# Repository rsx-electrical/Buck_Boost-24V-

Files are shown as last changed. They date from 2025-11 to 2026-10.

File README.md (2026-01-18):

# Buck_Boost
Designed to provide a regulated 24V output from a 6S (24V nominal) battery pack with an input range of about 19–25V.
Intended for use in a rover system powering comms hardware (TpLink POE; JETSON AGX ORIN).

# Workflow
1. Message Discord that you are working in the repo. Nobody else can work on it once you message.
2. `git clone git@github.com:rsx-electrical/Buck_Boost-24V-.git`
3. Edit 4_switch_Buck_Boost
4. Edit the README in 4_switch_Buck_Boost to describe what your commit does and why the changes were made.
5. Save a zip file version of your finished work into History Folder. 
- File should named `<date/time>_<name>_<brief_description_of_changes>`
5. Stage the files you want to commit. See "How to commit changes" bellow. 
6. `git commit -m <commit message>`
7. `git push`
8. Yay:). You are done

# Specs 
Vin: 19–25V (6S Li-ion pack)
Vout: 24V nominal
Estimated power: 100W total (More than sum of both loads, some margin for overhead and future changes)

# Notes
Design is still in development; input range, component choices, and power ratings may change. Focus is on stable 24V output, good efficiency, and reliable operation in a mobile rover environment.Future updates will include board revisions, layout improvements, and performance testing.

# How to commit changes
A file with changes can be in one of three states: untracked, modified, or staged. Only staged files are included in the next commit. 
- `git status`: command to see the status of the files you have modified
## Staged files
Staged changes are changes in files that have been marked in git to be included in the next commit. The section labeled "Changes to be committed" in git status shows these staged files.
If you stage a file and then make additional changes to it, those new changes are not staged and will not be included in the next commit. To include them, you need to stage the file again.
- `git add <file_name> `: command to stage a file
- `git add . `: stage all files with changes in them. Be careful as this will also stage untracked files which often we do not want to be staged. 
- `git restore --staged <file>` : command to unstage a file
## Tracked Files
Tracked files are files that git is already monitoring for changes, meaning they were previously committed and git keeps track of any modifications to them. 
## Untracked files
Untracked files are files in your working directory that Git does not yet know about. These are sometimes autogenerated files or files for certain settings in your local repo. An example on a Mac is .DS_Store. This .DS_Store file s a hidden file created by macOS in folders to store custom metadata about that folder, like icon positions, view settings, and window size. This is not a file that we want pushed to the remote repository.

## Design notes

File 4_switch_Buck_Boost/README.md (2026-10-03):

# Purpose of readme

This README describes each commit made to the `4_switch_Buck_Boost folder`. Add the most recent changes at the top, but below this "Purpose of readme" section.
Each commit section title in this README should follow this format: `Date, Name, Title of Commit`

## 10-02 William -- SW1, GND, Vout, pores

Draw and filled all the pores above along with the vias.

## 09-22 Maria -- Rsense footprint

Added Littelfuse L4CL2512 footprint for the sensing resistors. Reangered power path to accommodate size change in new resistor and inductor footprints.

## 09-20, William -- 4 Layers GND and GNDA plane

Made all the 4 Layers, Top-GND&GNDA-Vin-GND. Connected both GND and GNDA together thorugh a via and shorted resistor to prevent DRC error. Has connected all the vias in analog stage.

## 09-19, William -- Update footprint, Analog traces

Updated FETs symbols footprints, Inductor footprints, Connect traces for analog stage

## 09-12, Maria -- Reverse Polarity Protection

Added reverse polarity protection to the schematic and layout. Placed between the fuse and vin.

## 07-17, Anthony -- Template Starting Changes

Went ahead and hunkered down on some more final changes to the analog component placement, providing a tighter, more optimized orientation for building traces, closer/more compact. Def mess around with them if need be, esp the gate driver series resistors, those can go wherever you want, just pls keep the BOOTstrap caps as close as possible. With placement of analog passive components, gonna like draw gate signal traces as copper pours, up to discretion of later design review. Additionally, settled on shunt footprint/placement without compromising hot loop layout (best we gonna do, had to sacrifice snub filter, but this is optional, pick them up later). And, upgraded inductor footprint to be more 'on-brand' with the power inductors you're likely gonna find for the necessary L (uH) values that 55V/0.55A, 12V/5A are gonna demand. Please feel more than free to change any footprints you see fit. Also, omitted the fan control aux circuit, this is gonna be external to the buck-boost pcb. TLDR: slightly prepared everything to turn this 24V buck-boost into a template PCB for bucking/boosting and buck-boosting for 5V,12V,24V, and 55V.

## 07-03, Maria -- Passive Components, Controller and Auxiliary Circuits

Feedback from the June 3rd commit was that the passive component circuits should be closer to the controller. There is no need to have them so spread out and close to the power path as it should be good to have a trace to the power path. This update moves the feedback circuit, enable circuit and passive components for the controller to be closer to the controller. This update adds traces for these circuits (traces for within these Passive Components and Auxiliary Circuits only) as well as two pores for GNDA and GND (GND pore is the GND for the enable circuit). Please note that I know that the edges of these pores are rough. Turns out I am kinda sucky at drawing out pores. Also not there is no vias added. I am going to assume that these will be added once we agree with the component placement.

## 06-03, Maria -- Passive Components, Controller and Auxiliary Circuits

Added the passive components, controller and auxiliary Circuits to the power path

## 05-23, Maria -- First Attempt at power path

Uhm so this is written on June 3rd because I forgot. Soooooo yeah basically the title, first attempt at full power path.

## 04-03, William -- PCB components placement

Tried to minimize the Hot loops, further optimization may be required

## 03-17, Anthony -- Additional revisions on Schematic for Smooth Layout design for yall

Want to make layout go as smoothly as possible, so just went ahead and ensured all components had appropiate footprints. Also added NTC (temp control) for fan control using heat probe.

## List of stuff

-Added filter caps to Vin and Vout pin connections to LT8390

-Adjusted for larger Cout over Cin to reflect calculated sizing demands.

-Changed Inductor footprint for better saturation current rating/Irms rating, previous one was way to close to our shit, plus this footprint is way more streamlined imo

-Opt to use different footprint for shunt, kicad-preloads are fucking stinky uh uh (DOWNLOAD AND IMPORT SYMBOL AND FOOTPRINT PLEASE: https://www.snapeda.com/parts/KRL3216T4-M-R003-F-T1/Susumu/view-part/ )

-EN/UVLO needs voltage divider network for proper ENABLE, so adjusted level shifter circuit for ~1.2V to be seen at pin EN/UVLO, but still programs for undervoltage lockout when reach ~16V or so, good shutoff conditions in case BMS fucks us somehow -- It's a mandatory feature not preprogrammed like a lot of the TI chips are.

-Better probing points for observing ripple, PWM, or general signals (3 kinds of probe footprints). M3 Mounting holes added as well and dedicated Net tie for GNDA and GND (fuck with footprint if need be)

-Heatsink gonna be adhesive, fuck mounts, also made it an option to use osc freq or triangle spreading +/- 15%. Triangle spread usually better, but can introduce greater voltage ripple so we can place with it using jumper cap and 2x2 head conn setup.

-NTC for temp control fan will prob be wire that sits and probes heatsink, so just a CONN for now, we'll see, up to ya'll.

-All connections on schematic should roughly agree with where they'll go on layout (ie. BST caps near chip and not power stage)

-SMD trimmers, not bulky n shit (THT or SMD, if going near chip, SMD, if away from chip, THT/SMD).

-Snub filter 0805 caps, larger caps capable of handling transient response from fets way better than 402 or 603 so yeye, also shorter fuse holders too.

## 03-14, Anthony -- Final Check on shit

All pin connections/sizing good -- ready for layout

## 03-14, Maria Finish up pins and make it look pretty

I tried to make it look prettier. I may have failed at that but I finished up the pins;).

## 03-07, William, FeedBack loop trimmer and decoupling capacitor addition

Add a trimmer to ensure precise FB voltage of 1V, and a safety margin during tuning. Add Decoupling capacitor for stabilizing voltage.

## 03-06, Maria, LT8390 Pins

To be quite honest the most important part of this commit is probably this readme where I am documenting all of the questions I have about these pins. This commit is mostly my best guess. I hope to get clarification this Saturday ;).

### RT pin

This pin should have a resistor of 75kOhms attached to it. Question is should we have a potentiometer to ensure that we can tune to 75kOhms as all resistors will have some range of error on the resistance value.

### SS pin

All of the example applications have a value of 0.1u F. I don't understand how we determine the minimum soft-start time that we want. We don't add a resistance here because we want to hiccup safety mode, not latch off or keep running mode.

### Vc pin

I am so lost, I don't know my up from down for this pin.

### PGOOD pin

This pin is smth we could connect to an external microcontroller as indicator that the voltage has successfully reached its target. I don't think that this will probably be used. However connect to INTVcc with 100k ohms so that pin is pulled low when the FB pin is within �10 percent of the final regulation voltage. Maybe down the line we will want to connect it to smth, we could leave it hanging if we wanted. A value of 100kohms is used because that is used in all of the example application circuits.

### INTVcc pin

Tie to 4.7uF ceramic capacitor as instructed.

### SYNC/SPREAD

We don't want an external source for the switching. I think we probably want to have the mode with the 15 percent spread around internal oscillator frequency to ensure no sudden noise peaks. Tie this pin to INTVcc.

## 03-05, Maria, Capacitors !!!

Thank you Anthony for the document about filtering ringing and ripple!!! The document helped with this section a lot. Also thank you to the LT890 data sheet for going through a bit about Cin and Cout capacitances.

### Ringing Frequency

Ringing frequency of 75MHz-143MHz. 22nF will filter 30MHZ-100MHz range and 4.7nF will filter 100+MHz range. In a 4-switch buck-boost, the "Active Switching Side" moves depending on the mode (Buck or Boost). Therefore a 22 nF + 4.7 nF stack on required on both the Input and Output power rails to stay protected. At the high frequencies that ringing occurs at, the 15uH inductor between the two switching nodes is 2*pi*freq\*(15e-6). For a frequency of 100MHz this comes to an impedance of 9.5KOhms. Maybe we can consider using snub circuits on the switching nodes? May not be required as power rails are protected.

### Bulk Capacitors

Calculations for the following are seen on this spreadsheet under the Capacitance Values tab: https://docs.google.com/spreadsheets/d/1GE4mJHaV0VTMqPT8AXjkSjW_NcW0vJ0DrAooZ-j17pU/edit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

#### Cout

We want the output ripple to be at most 2 percent of the output voltage which is 0.480V. The output capacitance required to have this output ripple under boost conditions is at least 5.21uF and under buck conditions at least a 0.781uF output capacitance is required. To account for the Boost Right-Half-Plane Zero phenomenon a minimum of 57.9uF output capacitance is required. To account for voltage undershoot an output capacitance of 1.46uF is required. Therefore for the circuit to be functional an output capacitance of at least 57.9uF is required. We want low ESR. Two capacitances of 33uF can be used.

#### Cin

A Cin of at least 1.14uF is required to maintain under a input voltage ripple of 0.512V. However the input capacitance network should support a Irms current of Iout(max)/2 (see pg. 21 of LT8390 data sheet). No capacitor that small can support that large of a current. We also want a very small ESR. Therefore we should have larger capacitance values in parallel to split the current and lower ESR. For electrolytic capacitors that have smaller values their ESR is very large. Is it better to have only ceramic at the beginning. For now, I am going to put a placeholder value of three 22nF electrolytic capacitors or Cin. This will lower ESR and provide required capacitance. Ask this Saturday which type of capacitor would be best here. I feel like it would be ceramic.
####Next Steps
Next steps would be determining the exact capacitors required. Most of this is gonna be a fight of finding capacitors with low ESRs. If all falls apart can just use capacitors with higher values and have more in parallel to lower ESR (generally larger value electrolytic capacitors have lower ESRs). I am uncertain if we are just gonna use capacitors we have in stock. Smth I will have to ask Anthony.

## 02-27, Maria, High Side Switch

2N7002K: rsx nmos
BSS83P: rsx pmos only has Vds of 30V. rsx pmos is cutting it close because our vin can be 25ish. Dangerous if there are any spikes in our Vin. Chosen because it has a Vds of -60V which is very safe.
R106&R105: The Vgs of the pmos (BSS83P) is +/- 20V. Having this voltage divide means that the gate of the pmos will be half the voltage of Vin. This will allow the pmos to turn on when required but have a Vgs range of 9V to 13V when the enable pin is on and it will be around 0 when the enable pin if off. These are aat least 1.46ll safe ranges.

### Next Steps

Find the spec for the LEDs that rsx has in stock. Find out what the input voltage we will get from the microcontroller. Use this information to determine the exact values for the resistors at the gate of the nmos.

### LTSpice Simulation

#### High Side Switch Vin is 25.6V

PMOS high-side switch LTSpice schematic with Vin of 25.6V



When the enable input coming from a microcontroller (enable_vin) is set high, the enable pin (en_pin) on the LT8390 is set high. When the enable input is set low, the enable pin on the LT8390 is set low as well.



The Vgs (Vpmos_gate - Vin) and Vds (Ven_pin - Vin) of the pmos. Vgs is safe within the maximum of +/- 20V. Vds is safe with a maximum of -60V.



The Vgs (Ven_pin) and Vds (Vnmos_drain) of the nmos. Vgs is safe within the maximum of +/- 20V. Vds is safe with a maximum of 60V.



pmos Id is rated for -0.33A, nmos is rated for 320mA. Currents are in a safe range.



#### High Side Switch Vin is 18V

PMOS high-side switch LTSpice schematic with Vin of 18V.



When the enable input coming from a microcontroller (enable_vin) is set high, the enable pin (en_pin) on the LT8390 is set high. When the enable input is set low, the enable pin on the LT8390 is set low as well.



The Vgs (Vpmos_gate - Vin), Vds (Ven_pin - Vin) and Id of the pmos. Vgs is safe within the maximum of +/- 20V. Vds is safe with a maximum of -60V. Id is safe as pmos is rated for -0.33A.



The Vgs (Ven_pin) and Vds (Vnmos_drain) of the nmos. Vgs is safe within the maximum of +/- 20V. Vds is safe with a maximum of 60V.



nmos current is good.



## 02-07, Maria, Reformat to be readable

Reformat to be split up into sections like the example Anthony gave us of a past boost converter. Input filtering capacitors with no values. They are placeholders. Values will need to be determined and number of capacitors will need to be determined.

## 02-05, Maria, connected power path to chip

Yeah I know title doesn't make sense. Added power path (MOSFETTS and inductor) to schematic. Connected FB. Vout/Vfb = 24. Chosen resistance values are (232 + 10)/10 =24.2. The ratio is correct; however, I assume these values may be changes for resistors rsx has in storage. 603 resistors are used because low power will flow through them. Shunt resistors are used for current sensing. Again these may be replaces with resistance values for resistors we already have. The math for these values can be found in the Google doc. Capacitors for the BST1 and BST2 are 2.5uC because gate charge of MOSFETTs are 2.5e-8C and the capacitance should be 100x the gate charge. Things needed to be talked about: do we want to use shunt resistors, and what resistors do we have in stock to choose from.

## 01-17, Anthony, added selection of res and caps

Basically just put in a couple of diff types of res and caps and their respective footprints (ceramic, polarized, shunt, basic shit that we'll prob use in the future, just pay attention to what each footprint corresponding to each symbol belongs to).

603 and 805 usually for IC filtering with 805 for larger analog symbols (LDOs) and 1206 usually for bulk cap filtering of noise at input/outputs. Polarized caps used for stabilizing voltage/reducing ripple/storing energy/etc.

603 and res up usually depend on power dissipation, with the shunt being the widest and likely used for current sensing, if choose to go down this route into design, may need to change footprint, the Vishay one is overpowered and like for 0.0001ohm applications, which is, nah.

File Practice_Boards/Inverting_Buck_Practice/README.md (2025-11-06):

# Inverting Buck Practice
Inverting Buck Board using MC33063AD topology for Inverting Regualtors (3V --> -2V)

First Iteration:
OldMariaInvertBuck

Made a couple of changes, aligned the gnd and vout terminals of the screw terminal and capacitor so at to have a cleaner and wider vout/gnd copper pour, with buck having a larger Iout>Iin, so less power less internally with potetnually larger current.

Also went ahead and drew all the passive components for the IC as closer to the main body of the chip as possible, this will come into greater importance later on when working with more complicated PWM controllers, espcially with analog traces, having as close of a connection for traces conducting in the mA order succombing to greater loss the longer the distance it has to travel to communicate with the IC.

Via placemnt centralized at the capacitor (input and output, with discharge into ground requiring the greatest degree of stitching with a return path to the bottom ground layer.

Edited Second Iteration:


Tried to make the board as tight and small as possible, the modified version is not the 'best' version. You don't hvae to make additional edits, but if you chose to you absolutely can, but regardless, where do you think the board can be improved and why? If you're not sure if there can be improvements, or feel unsure to the 'why?' part of the question, please let me know on the discord.

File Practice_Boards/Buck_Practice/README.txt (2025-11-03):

Place your current progress in this folder, and ping me when you do. I'll be able to view it and make comments, and you can pull it from the GitHub and continue with any additional work, and push your final iteration.

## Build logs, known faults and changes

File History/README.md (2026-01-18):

# Workflow
For every commit where 4_switch_Buck_Boost is changed a .zip file copy of the 4_switch_Buck_Boost must be saved in the History Folder.
Make sure the changes will appear in chronological order so have the names of the .zip file as `<date/time>_<name>_<brief_description_of_changes>`. 

<01-17/10:57 PM>_<Anthony>_<put in selection of caps and res we'll prob use, with their footprints>

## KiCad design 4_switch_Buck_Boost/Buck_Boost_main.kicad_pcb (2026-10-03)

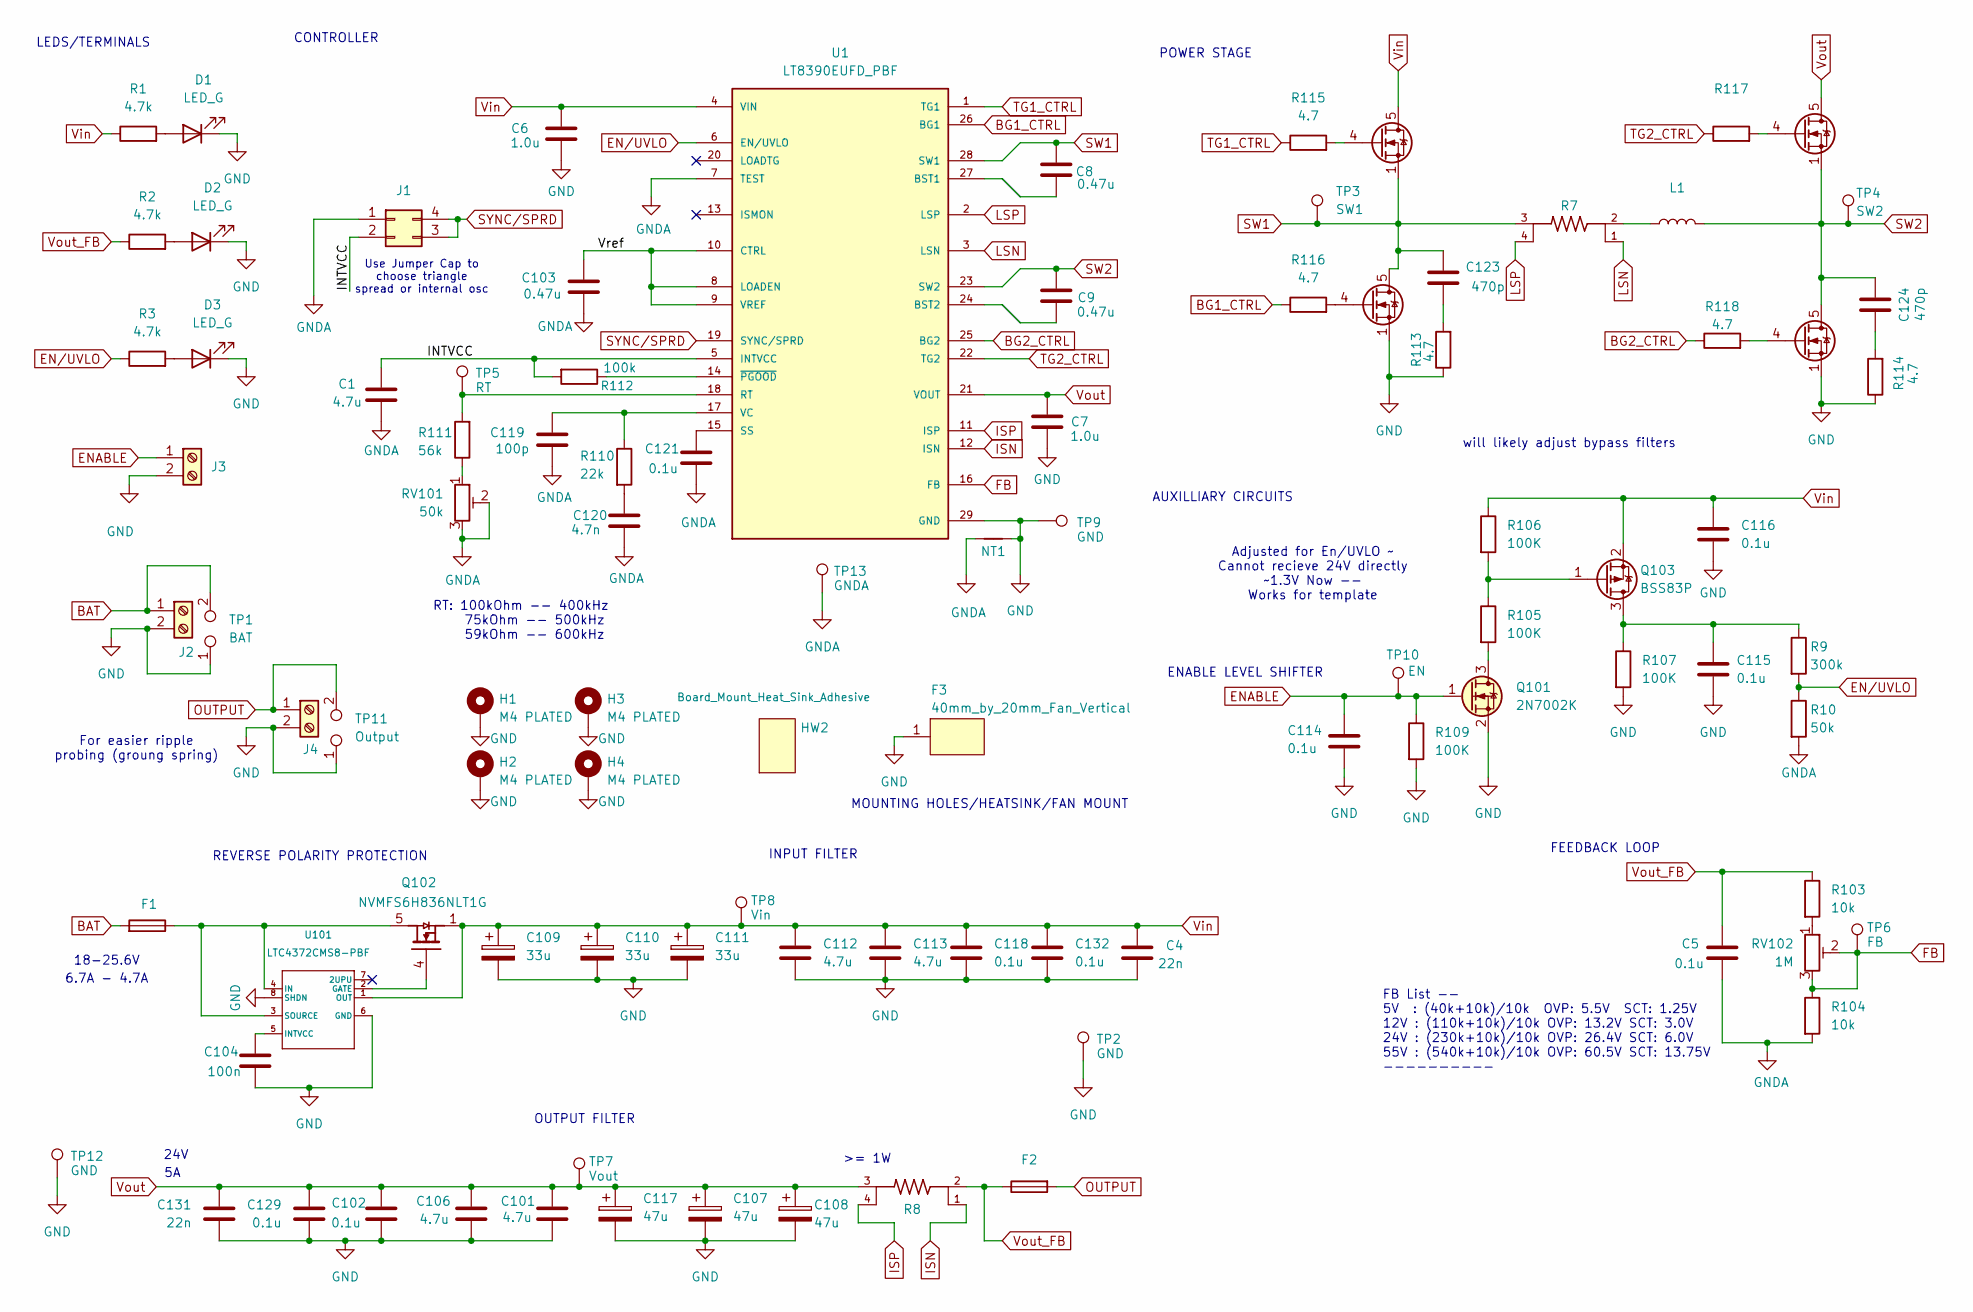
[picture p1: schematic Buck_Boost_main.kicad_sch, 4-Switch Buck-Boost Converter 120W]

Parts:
C1, C101, C106, C112, C113: 4.7u; C_0805_2012Metric
C4, C131: 22n; C_0603_1608Metric
C5, C102, C114, C115, C116, C118, C121, C129, C132: 0.1u; C_0603_1608Metric
C6, C7: 1.0u; C_0603_1608Metric
C8, C9, C103: 0.47u; C_0603_1608Metric
C104: 100n; C_0603_1608Metric
C107, C108, C117: 47u; CP_Elec_8x10.5
C109, C110, C111: 33u; CP_Elec_8x10.5
C119: 100p; C_0603_1608Metric
C120: 4.7n; C_0603_1608Metric
C123, C124: 470p; C_0805_2012Metric
D1, D2, D3: LED_G; LED_0805_2012Metric; MPN LTST-C170GKT
F1, F2: Fuse_Holder_Auto; Fuseholder_Blade_Mini_Keystone_3568; MPN 3568-10
F3: 40mm_by_20mm_Fan_Vertical; 40mmFan; MPN THA0412AD
H1, H2, H3, H4: M4 PLATED; MountingHole_3.2mm_M3_Pad_Via
HW2: Board_Mount_Heat_Sink_Adhesive; BDN10-3CB_A01; MPN BDN10-3CB/A01
J1: Conn_02x02_Counter_Clockwise; PinHeader_2x02_P1.00mm_Vertical
J2, J4: Screw_Terminal_2x5.08; Molex_0398800302; MPN 398800302
J3: Screw_Terminal_2x2.54; Wurth_691210910002; MPN 691210910002
L1: L_Bourns_SRP1770TA_16.9x16.9mm; MPN PQ2617BHA-150K
NT1: NetTie_2; NetTie-2_SMD_Pad0.5mm
Q101: 2N7002K; SOT-23; MPN 2N7002K-T1-E3
Q102: NVMFS6H836NLT1G; ONSemi_SO-8FL_488AA
Q103: BSS83P; SOT-23
Q104, Q105, Q106, Q107: BSC070N10LS5; TDSON-8-1
R1, R2, R3: 4.7k; R_0603_1608Metric
R7, R8: Littelfuse_L4CA0612_4Terminal; PARTREV N/A
R9: 300k; R_0603_1608Metric
R10: 50k; R_0603_1608Metric
R103, R104: 10k; R_0603_1608Metric
R105, R106, R107, R109: 100K; R_0603_1608Metric
R110: 22k; R_0603_1608Metric
R111: 56k; R_0603_1608Metric
R112: 100k; R_0603_1608Metric
R113, R114: 4.7; C_0805_2012Metric
R115, R116, R117, R118: 4.7; R_0603_1608Metric
RV101: 50k; Potentiometer_Bourns_3314G_Vertical
RV102: 1M; Potentiometer_Bourns_3314G_Vertical
TP1: BAT; TestPoint_2Pads_Pitch2.54mm_Drill0.8mm
TP2, TP9, TP12: GND; TestPoint_Pad_D1.0mm
TP3: SW1; TestPoint_Loop_D1.80mm_Drill1.0mm_Beaded
TP4: SW2; TestPoint_Loop_D1.80mm_Drill1.0mm_Beaded
TP5: RT; TestPoint_Pad_D1.0mm
TP6: FB; TestPoint_Pad_D1.0mm
TP7: Vout; TestPoint_Pad_D1.0mm
TP8: Vin; TestPoint_Pad_D1.0mm
TP10: EN; TestPoint_Pad_D1.0mm
TP11: Output; TestPoint_2Pads_Pitch2.54mm_Drill0.8mm
TP13: GNDA; TestPoint_Pad_D1.0mm
U1: LT8390EUFD_PBF; QFN50P500X400X80-29N; PARTREV C
U101: LTC4372CMS8-PBF; MS8_05-08-1660_ADI

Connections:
/INTVCC: C1.2, J1.2, R112.2, U1.5 (INTVCC)
/Vref: C103.2, U1.8 (LOADEN), U1.9 (VREF), U1.10 (CTRL)
BAT: F1.1, J2.1, TP1.2
BG1_CTRL: R116.1, U1.26 (BG1)
BG2_CTRL: R118.1, U1.25 (BG2)
ENABLE: C114.1, J3.1, Q101.1 (G), R109.1, TP10.1
EN/UVLO: R3.1, R9.2, R10.1, U1.6 (EN/UVLO)
FB: R104.1, RV102.2, RV102.3, TP6.1, U1.16 (FB)
GND: C4.2, C6.1, C7.1, C101.2, C102.2, C104.2, C106.2, C107.2, C108.2, C109.2, C110.2, C111.2, C112.2, C113.2, C114.2, C115.2, C116.2, C117.2, C118.2, C129.2, C131.2, C132.2, D1.1 (K), D2.1 (K), D3.1 (K), F3.1, H1.1, H2.1, H3.1, H4.1, J2.2, J3.2, J4.2, NT1.2, Q101.2 (S), Q106.1 (S), Q106.2, Q106.3, Q107.1 (S), Q107.2, Q107.3, R107.2, R109.2, R113.1, R114.1, TP1.1, TP2.1, TP9.1, TP11.1, TP12.1, U1.29 (GND), U101.6 (GND), U101.8 (SHDN)
GNDA: C1.1, C5.2, C103.1, C119.2, C120.2, C121.2, J1.1, NT1.1, R10.2, R104.2, RV101.2, RV101.3, TP13.1, U1.7 (TEST)
ISN: R8.1, U1.12 (ISN)
ISP: R8.4, U1.11 (ISP)
LSN: R7.1, U1.3 (LSN)
LSP: R7.4, U1.2 (LSP)
unnamed: C120.1, R110.2
unnamed: C123.2, R113.2
unnamed: C124.1, R114.2
unnamed: D1.2 (A), R1.2
unnamed: D2.2 (A), R2.2
unnamed: D3.2 (A), R3.2
unnamed: L1.1, R7.2
unnamed: Q101.3 (D), R105.2
unnamed: F1.2, Q102.5 (D), U101.3 (SOURCE), U101.4 (IN)
unnamed: Q102.4 (G), U101.2 (GATE)
unnamed: C115.1, Q103.3 (D), R9.1, R107.1
unnamed: Q103.1 (G), R105.1, R106.2
unnamed: Q104.4 (G), R115.2
unnamed: Q105.4 (G), R117.2
unnamed: Q106.4 (G), R118.2
unnamed: Q107.4 (G), R116.2
unnamed: R103.2, RV102.1
unnamed: R111.1, RV101.1
unnamed: C8.1, U1.27 (BST1)
unnamed: C9.1, U1.24 (BST2)
unnamed: R111.2, TP5.1, U1.18 (RT)
unnamed: C121.1, U1.15 (SS)
unnamed: C119.1, R110.1, U1.17 (VC)
unnamed: R112.1, U1.14 (~PGOOD)
unnamed: C104.1, U101.5 (INTVCC)
OUTPUT: F2.1, J4.1, TP11.2
SW1: C8.2, C123.1, Q104.1 (S), Q104.2, Q104.3, Q107.5 (D), Q107.6, Q107.7, Q107.8, R7.3, TP3.1, U1.28 (SW1)
SW2: C9.2, C124.2, L1.2, Q105.1 (S), Q105.2, Q105.3, Q106.5 (D), Q106.6, Q106.7, Q106.8, TP4.1, U1.23 (SW2)
SYNC/SPRD: J1.3, J1.4, U1.19 (SYNC/SPRD)
TG1_CTRL: R115.1, U1.1 (TG1)
TG2_CTRL: R117.1, U1.22 (TG2)
Vin: C4.1, C6.2, C109.1, C110.1, C111.1, C112.1, C113.1, C116.1, C118.1, C132.1, Q102.1 (S), Q102.2 (S), Q102.3 (S), Q103.2 (S), Q104.5 (D), Q104.6, Q104.7, Q104.8, R1.1, R106.1, TP8.1, U1.4 (VIN), U101.1 (OUT)
Vout: C7.2, C101.1, C102.1, C106.1, C107.1, C108.1, C117.1, C129.1, C131.1, Q105.5 (D), Q105.6, Q105.7, Q105.8, R8.3, TP7.1, U1.21 (VOUT)
Vout_FB: C5.1, F2.2, R2.1, R8.2, R103.1

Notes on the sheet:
LEDS/TERMINALS
Adjusted for En/UVLO ~ Cannot recieve 24V directly ~1.3V Now -- Works for template
INPUT FILTER
24V
REVERSE POLARITY PROTECTION
FB List -- 5V : (40k+10k)/10k OVP: 5.5V SCT: 1.25V 12V : (110k+10k)/10k OVP: 13.2V SCT: 3.0V 24V : (230k+10k)/10k OVP: 26.4V SCT: 6.0V 55V : (540k+10k)/10k OVP: 60.5V SCT: 13.75V ----------
18-25.6V
AUXILLIARY CIRCUITS
Use Jumper Cap to choose triangle spread or internal osc
RT: 100kOhm -- 400kHz 75kOhm -- 500kHz 59kOhm -- 600kHz
POWER STAGE
For easier ripple probing (groung spring)
FEEDBACK LOOP
OUTPUT FILTER
ENABLE LEVEL SHIFTER
will likely adjust bypass filters
CONTROLLER
6.7A - 4.7A
>= 1W
MOUNTING HOLES/HEATSINK/FAN MOUNT

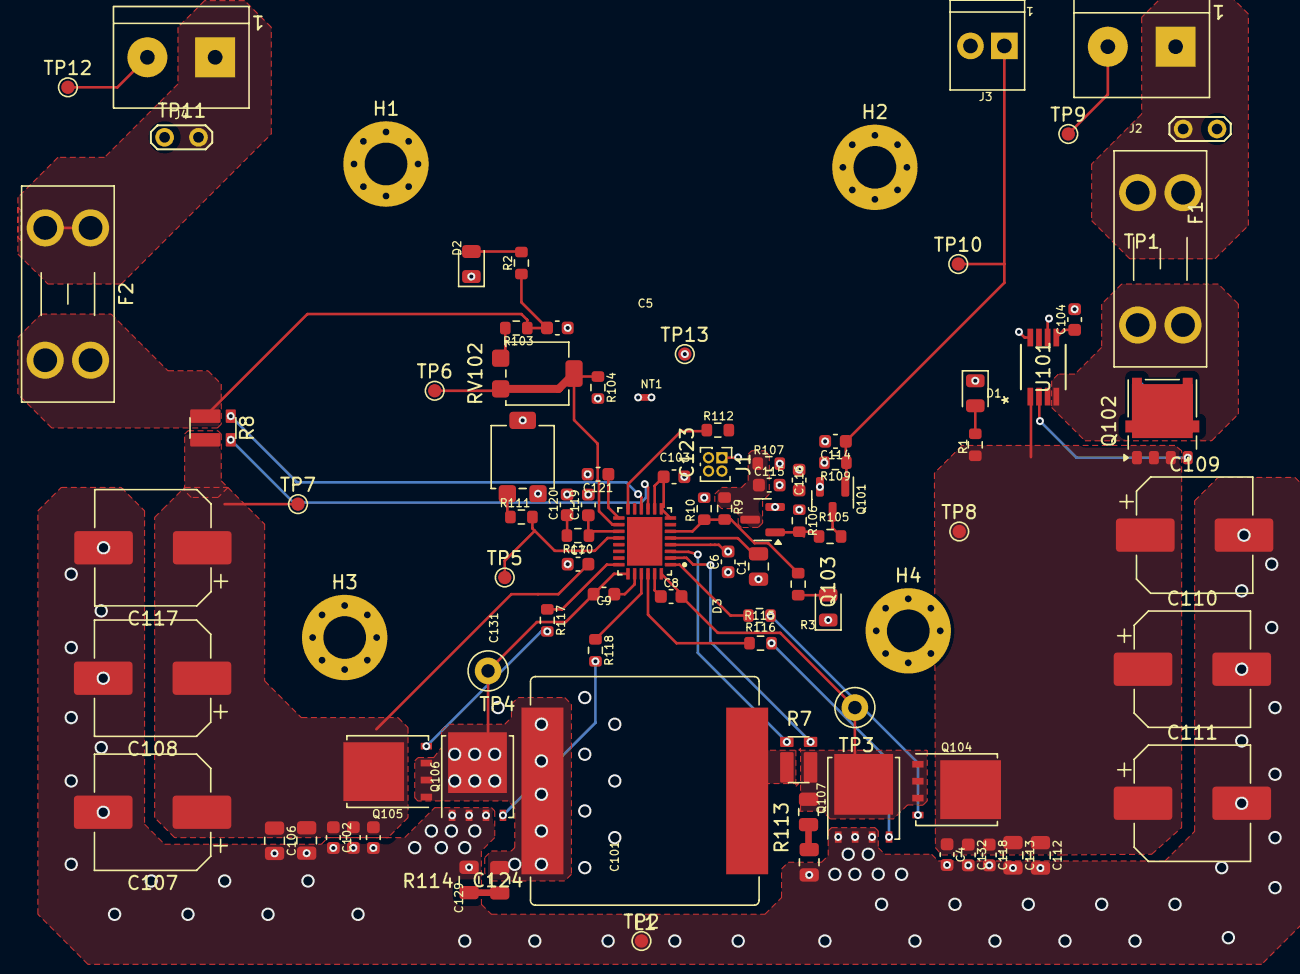
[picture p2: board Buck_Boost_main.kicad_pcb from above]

Board: 4 copper layers, 95 parts (0 on the bottom side), 48 nets.

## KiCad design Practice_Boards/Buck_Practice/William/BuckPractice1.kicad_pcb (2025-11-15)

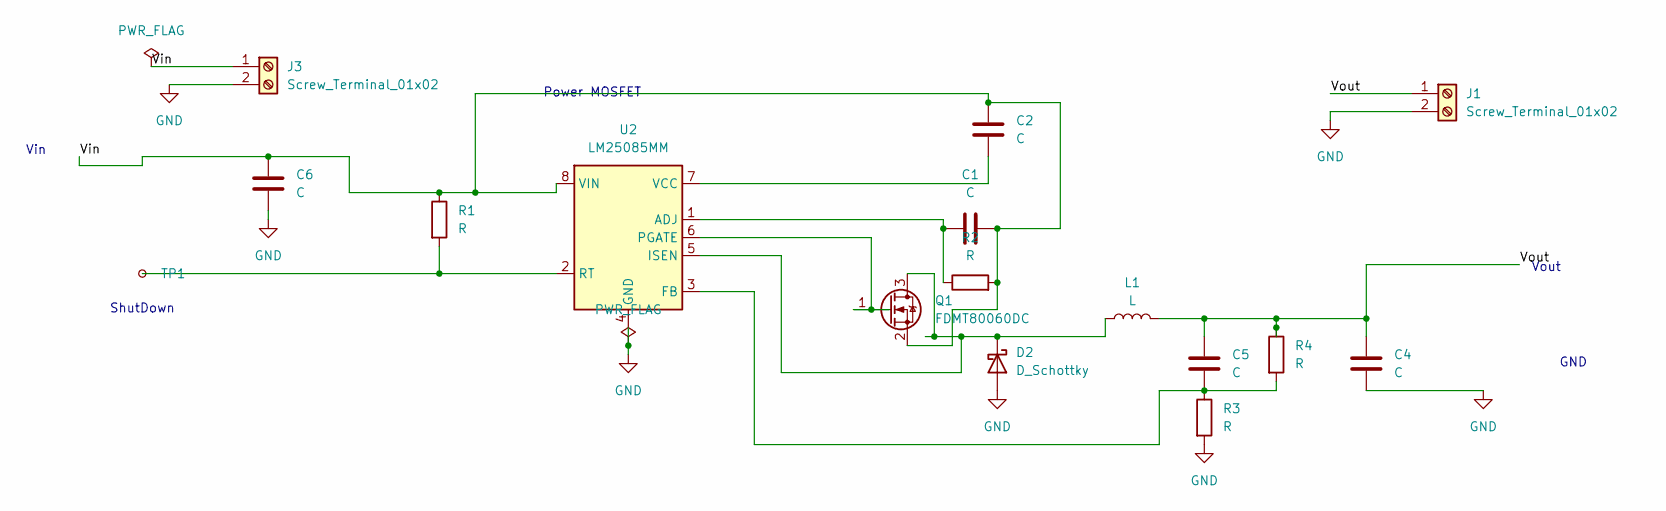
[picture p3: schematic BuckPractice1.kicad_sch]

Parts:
C1, C5: C; C_0805_2012Metric; MPN CL21B105KBFNNNE
C2, C4, C6: C; C_Elec_10x10.2
D2: D_Schottky; D_SMA
J1, J3: Screw_Terminal_01x02; TerminalBlock_4Ucon_1x02_P3.50mm_Vertical
L1: L; L_Coilcraft_XAL1350-XXX
Q1: FDMT80060DC; PQFN_8x8
R1, R2, R3, R4: R; R_0805_2012Metric
TP1: TestPoint_Small; TestPoint_Pad_D1.0mm
U2: LM25085MM; MSOP-8_3x3mm_P0.65mm

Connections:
/Vin: C1.2, C2.1, C6.1, J3.1, Q1.2 (S), R1.1, R2.2, U2.8 (VIN)
/Vout: C4.1, C5.2, J1.1, L1.2, R4.1
GND: C4.2, C6.2, D2.2 (A), J1.2, J3.2, R3.2, U2.4 (GND)
unnamed: D2.1 (K), L1.1, Q1.3 (D), U2.5 (ISEN)
unnamed: Q1.1 (G), U2.6 (PGATE)
unnamed: C1.1, R2.1, U2.1 (ADJ)
unnamed: C5.1, R3.1, R4.2, U2.3 (FB)
unnamed: R1.2, TP1.1, U2.2 (RT)
unnamed: C2.2, U2.7 (VCC)

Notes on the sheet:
GND
Vin
Vout
Power MOSFET
ShutDown

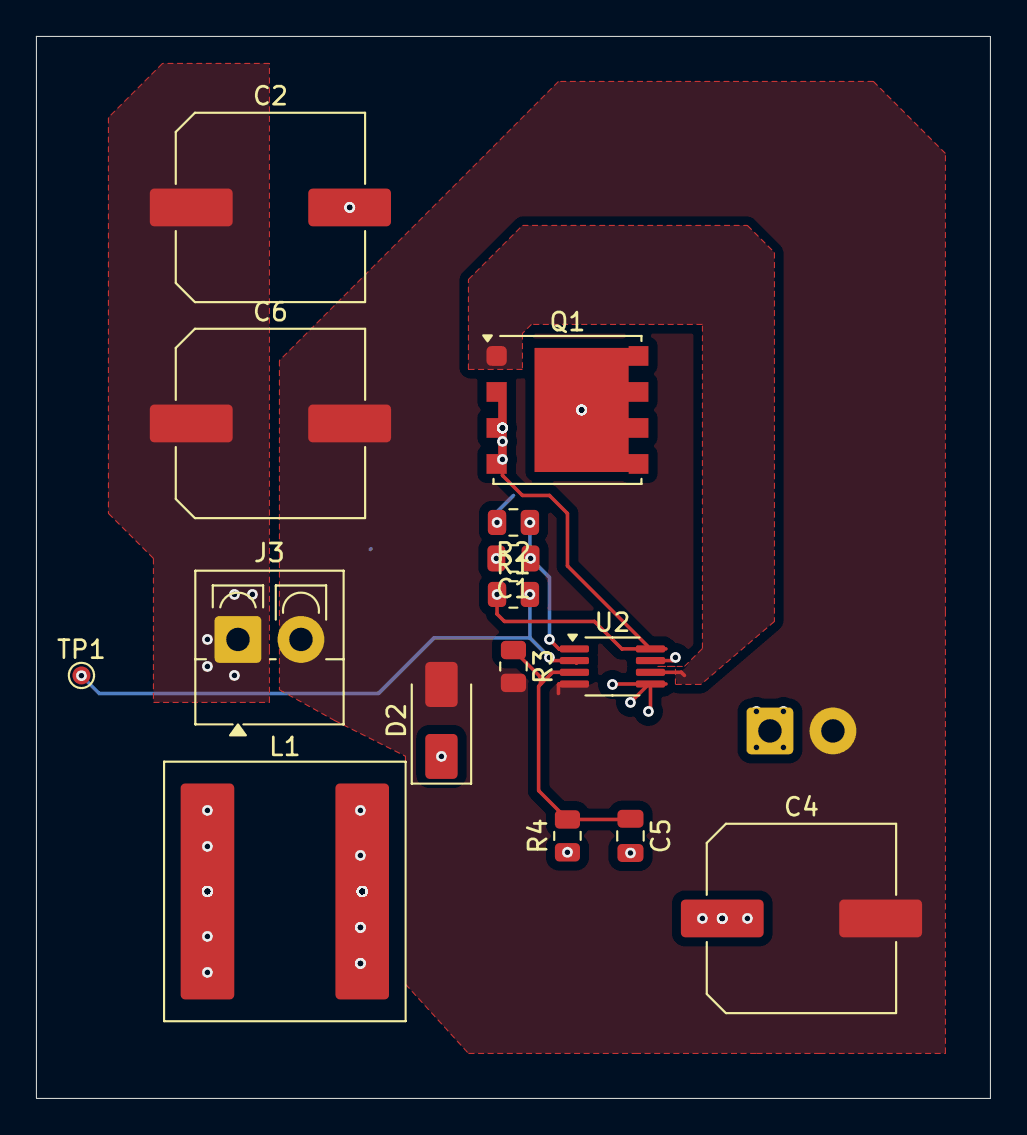
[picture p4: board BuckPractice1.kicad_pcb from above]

Board: 2 copper layers, 53.0 x 59.0 mm, 16 parts (1 on the bottom side), 9 nets.

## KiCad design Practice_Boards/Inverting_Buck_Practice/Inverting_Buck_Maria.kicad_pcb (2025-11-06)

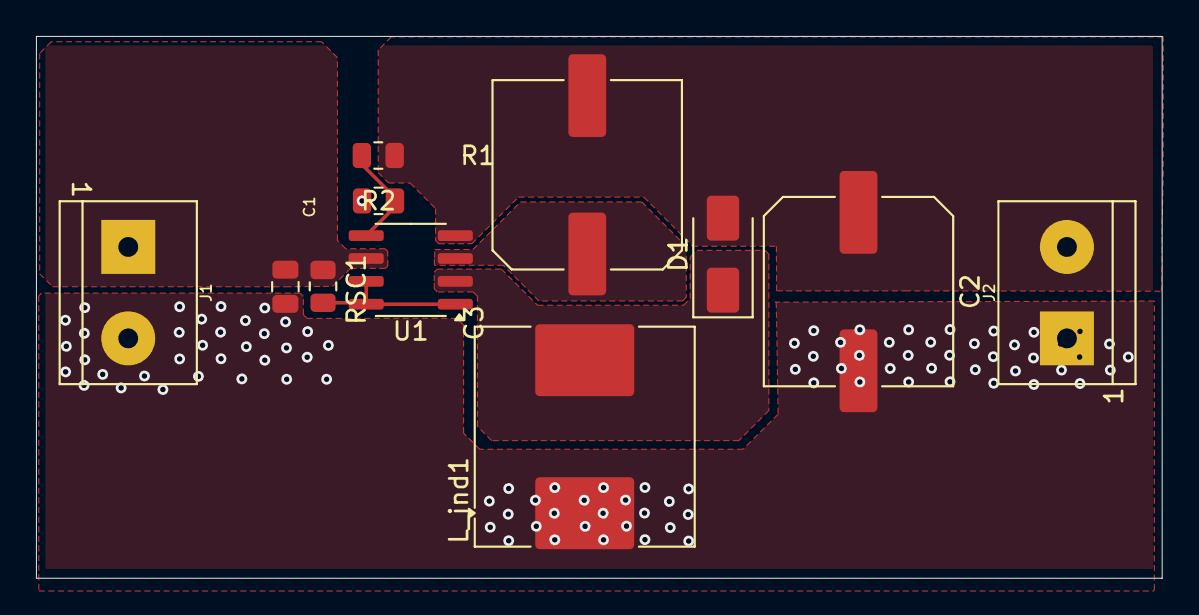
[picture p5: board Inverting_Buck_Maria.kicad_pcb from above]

Board: 2 copper layers, 62.5 x 30.1 mm, 11 parts (0 on the bottom side), 7 nets.

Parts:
C1: 100u; C_0805_2012Metric
C2: 0.36m; C_Elec_10x10.2
C3: 1.8n; C_Elec_10x10.2
D1: D_Schottky; D_SMA
J1, J2: Screw_Terminal_2x5.08; Molex_0398800302
L_ind1: 0.18m; L_Coilcraft_MSS1260H-XXX
R1: 1500; R_0805_2012Metric
R2: 900; R_0805_2012Metric
RSC1: 0.42; R_0805_2012Metric
U1: MC33063AD; SOIC-8_3.9x4.9mm_P1.27mm

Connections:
/V_in: C1.1, J1.1, RSC1.1, U1.6 (Vin)
/V_in_after_Rsc: RSC1.2, U1.1 (SwC), U1.7 (Ipk), U1.8 (DC)
/V_ind: D1.1 (K), L_ind1.2, U1.2 (SwE)
/V_out: C2.1, C3.2, D1.2 (A), J2.2, R1.1, U1.4 (GND)
/V_volt_divider: R1.2, R2.1, U1.5 (Vfb)
GND: C1.2, C2.2, J1.2, J2.1, L_ind1.1, R2.2
unnamed: C3.1, U1.3 (TC)

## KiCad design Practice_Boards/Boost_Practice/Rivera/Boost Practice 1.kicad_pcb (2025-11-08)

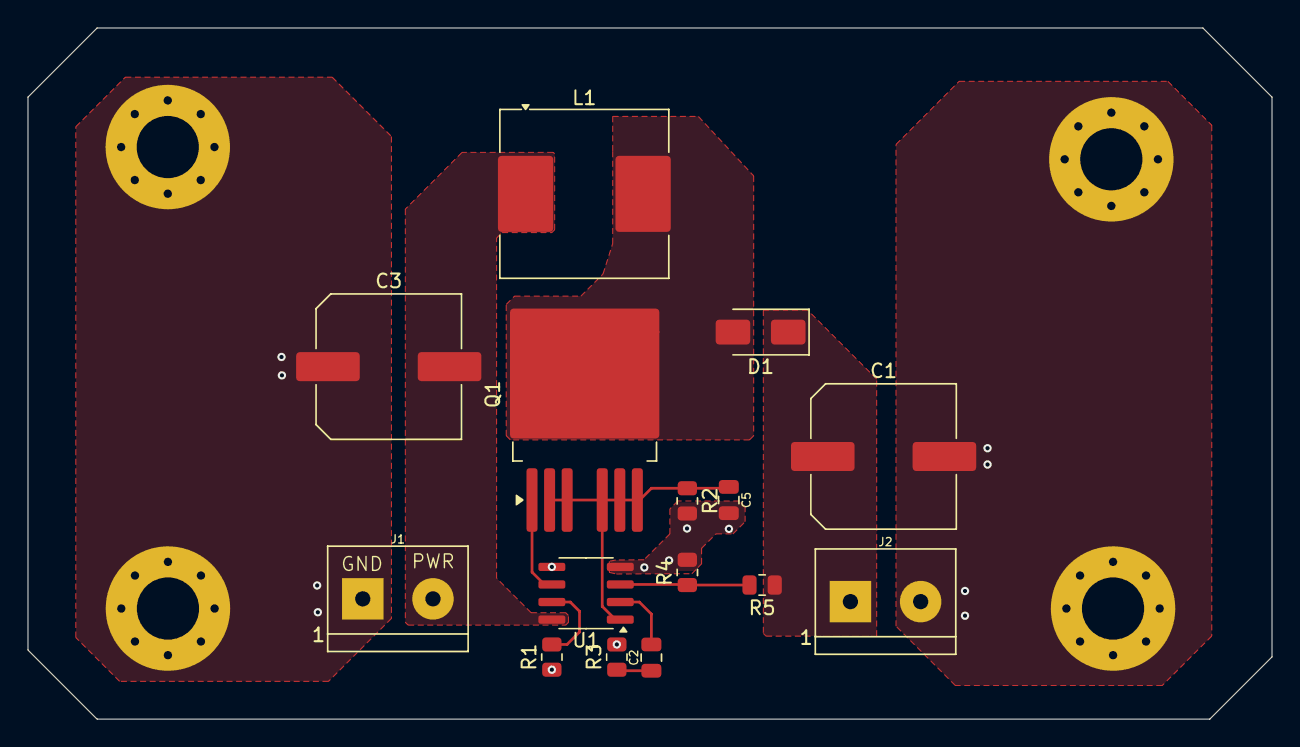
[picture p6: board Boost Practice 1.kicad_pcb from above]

Board: 2 copper layers, 90.0 x 50.0 mm, 19 parts (0 on the bottom side), 10 nets.

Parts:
C1, C3: 100uF; C_Elec_10x10.2
C2: 22nF; C_0805_2012Metric
C5: 0.01uF; C_0805_2012Metric
D1: D_Schottky; D_SMA
H1, H2, H3, H4: M4 PLATED; MountingHole_4.5mm_Pad_Via
J1, J2: Screw_Terminal_2x5.08; Molex_0398800302
L1: 10uH; L_Coilcraft_MSS1260H-XXX
Q1: IPB180N10S4-02; TO-263-6
R1: 40k; R_0805_2012Metric
R2: 0.025; R_0805_2012Metric
R3: 4.7k; R_0805_2012Metric
R4: 20k; R_0805_2012Metric
R5: 60k; R_0805_2012Metric
U1: LM3478MA; SOIC-8_3.9x4.9mm_P1.27mm

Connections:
/Vin: C3.2, J1.2, L1.1, U1.8 (V_{IN})
/Vout: C1.1, D1.1 (K), J2.1, R5.1
GND: C1.2, C3.1, C5.2, H1.1, H2.1, H3.1, H4.1, J1.1, J2.2, R1.1, R2.2, R3.2, R4.2, U1.4 (AGND), U1.5 (PGND)
unnamed: C2.1, R3.1
unnamed: D1.2 (A), L1.2, Q1.4 (D)
unnamed: Q1.1 (G), U1.6 (DR)
unnamed: C2.2, U1.2 (COMP)
unnamed: R1.2, U1.7 (FA/SD)
unnamed: R4.1, R5.2, U1.3 (FB)
unnamed: C5.1, Q1.2 (S), Q1.3 (S), Q1.5 (S), Q1.6 (S), Q1.7 (S), R2.1, U1.1 (I_{SEN})

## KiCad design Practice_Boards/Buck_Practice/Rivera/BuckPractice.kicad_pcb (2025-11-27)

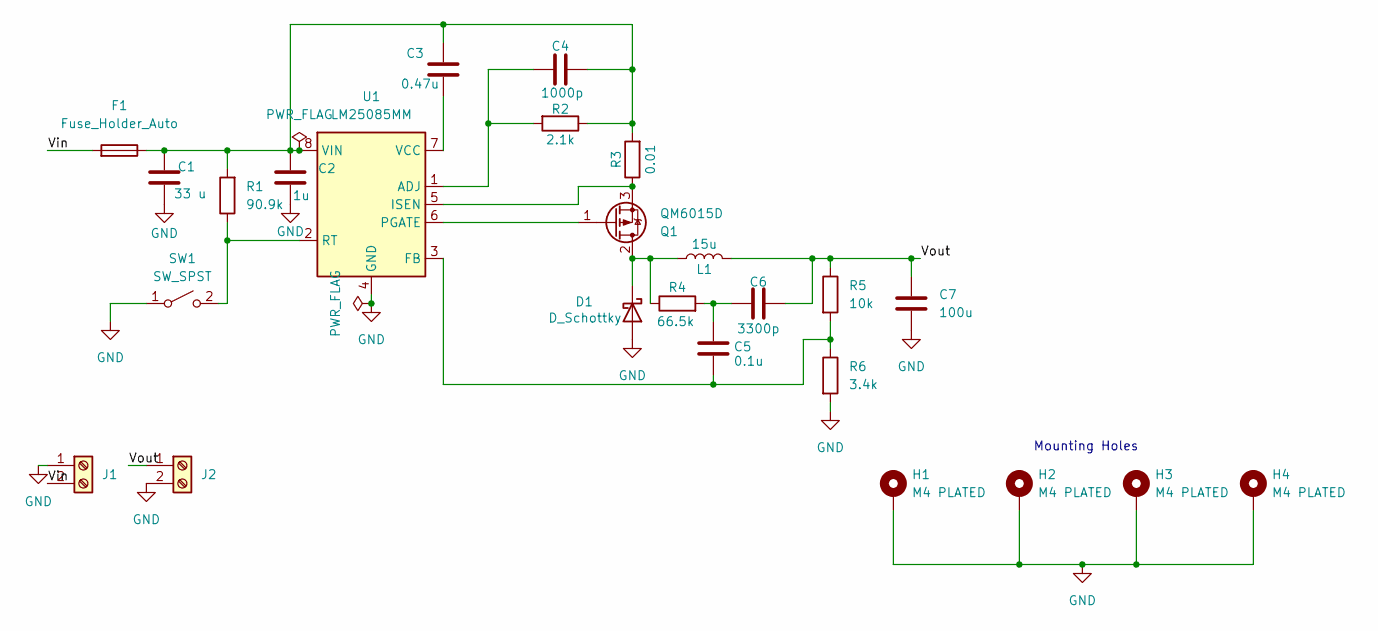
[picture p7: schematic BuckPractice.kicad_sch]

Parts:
C1: 33 u; C_Elec_10x10.2
C2: 1u; C_0805_2012Metric; MPN CL21B105KBFNNNE
C3: 0.47u; C_Elec_10x10.2
C4: 1000p; C_0805_2012Metric; MPN CL21B105KBFNNNE
C5: 0.1u; C_0805_2012Metric; MPN CL21B105KBFNNNE
C6: 3300p; C_0805_2012Metric; MPN CL21B105KBFNNNE
C7: 100u; C_Elec_10x10.2
D1: D_Schottky; D_SMA
F1: Fuse_Holder_Auto; FUSE_3568-10; MPN 3568-10
H1, H2, H3, H4: M4 PLATED; MountingHole_4.5mm_Pad_Via
J1, J2: Screw_Terminal_2x5.08; Molex_0398800302; MPN 398800302
L1: 15u; L_Coilcraft_XAL1350-XXX
Q1: QM6015D; TO-252-2
R1: 90.9k; R_0805_2012Metric; MPN RMCF0603ZT0R00
R2: 2.1k; R_0805_2012Metric; MPN RMCF0603ZT0R00
R3: 0.01; R_0805_2012Metric; MPN RMCF0603ZT0R00
R4: 66.5k; R_0805_2012Metric; MPN RMCF0603ZT0R00
R5: 10k; R_0805_2012Metric; MPN RMCF0603ZT0R00
R6: 3.4k; R_0805_2012Metric; MPN RMCF0603ZT0R00
SW1: SW_SPST; PinHeader_1x02_P2.54mm_Vertical
U1: LM25085MM; MSOP-8_3x3mm_P0.65mm_DL

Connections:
/Vin: F1.1, J1.2
/Vout: C6.2, C7.1, J2.1, L1.2, R5.1
GND: C1.2, C2.2, C7.2, D1.2 (A), H1.1, H2.1, H3.1, H4.1, J1.1, J2.2, R6.2, SW1.1 (A), U1.4 (GND)
unnamed: C5.1, C6.1, R4.2
unnamed: D1.1 (K), L1.1, Q1.2 (D), R4.1
unnamed: Q1.1 (G), U1.6 (PGATE)
unnamed: Q1.3 (S), R3.1, U1.5 (ISEN)
unnamed: R1.1, SW1.2 (B), U1.2 (RT)
unnamed: C4.2, R2.2, U1.1 (ADJ)
unnamed: C5.2, R5.2, R6.1, U1.3 (FB)
unnamed: C3.2, U1.7 (VCC)
unnamed: C1.1, C2.1, C3.1, C4.1, F1.2, R1.2, R2.1, R3.2, U1.8 (VIN)

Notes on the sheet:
Mounting Holes

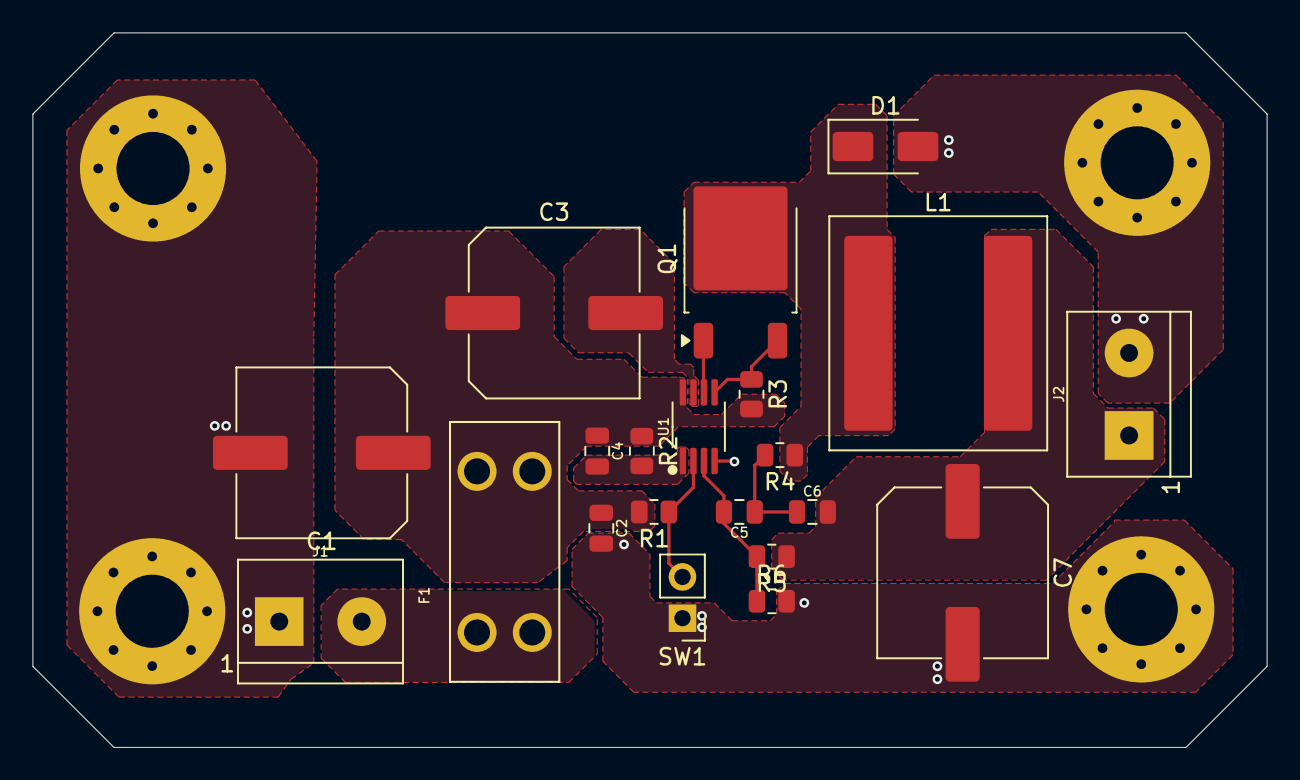
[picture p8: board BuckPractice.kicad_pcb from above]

Board: 2 copper layers, 76.0 x 44.0 mm, 25 parts (0 on the bottom side), 12 nets.

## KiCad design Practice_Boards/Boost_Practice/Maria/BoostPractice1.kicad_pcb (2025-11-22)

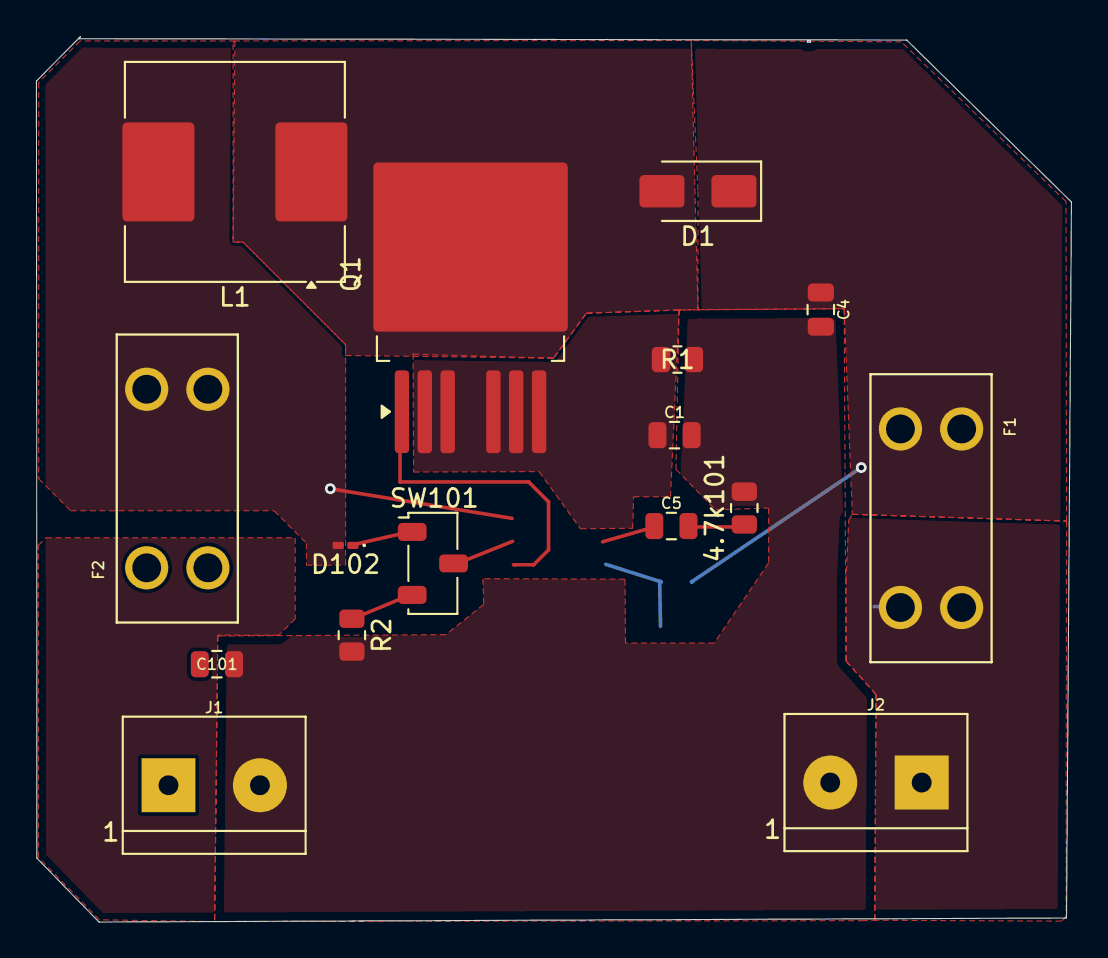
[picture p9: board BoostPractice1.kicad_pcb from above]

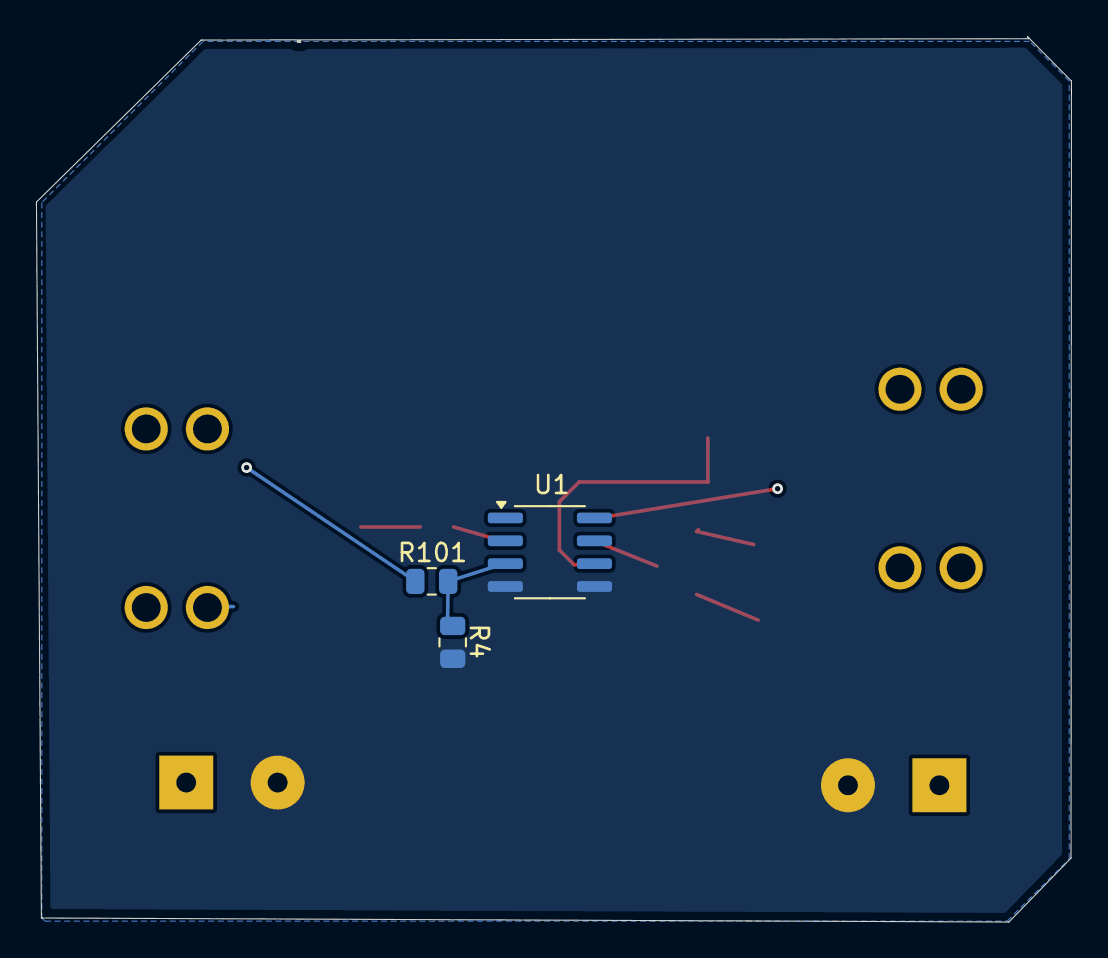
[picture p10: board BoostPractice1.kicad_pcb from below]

Board: 2 copper layers, 57.5 x 49.2 mm, 19 parts (3 on the bottom side), 14 nets, no tracks yet.

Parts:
4.7k101: R; R_0805_2012Metric
C1: 0.01u; C_0805_2012Metric
C4, C101: 100u; C_0805_2012Metric
C5: 22n; C_0805_2012Metric
D1: D_Schottky; D_SMA
D102: LED; LED_0201_0603Metric_Pad0.64x0.40mm_HandSolder
F1, F2: Fuse_Holder_Auto; FUSE_3568-10
J1, J2: Screw_Terminal_2x5.08; Molex_0398800302
L1: 10u; L_Coilcraft_MSS1260H-XXX
Q1: IPB180N10S4-02; TO-263-6
R1: 0.025; R_0805_2012Metric
R2: 40k; R_0805_2012Metric
R4: 20k; R_0805_2012Metric
R101: 60k; R_0805_2012Metric
SW101: SW_Nidec_CAS-120A1; Nidec_Copal_CAS-120A
U1: LM3478MA; SOIC-8_3.9x4.9mm_P1.27mm

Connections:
/COMP: C5.1, U1.2 (COMP)
/DR: Q1.1 (G), U1.6 (DR)
/Isen: C1.1, Q1.2 (S), Q1.3 (S), Q1.5 (S), Q1.6 (S), Q1.7 (S), R1.1, U1.1 (I_{SEN})
/V_FA/SD: SW101.2 (B), U1.7 (FA/SD)
/V_FB: R4.1, R101.2, U1.3 (FB)
/V_LED_ON: D102.1 (K), SW101.1 (C)
/V_boost_mode: R2.1, SW101.3 (A)
/V_ind: D1.2 (A), L1.1, Q1.4 (D)
/Vin: C101.1, F2.1, J1.1
/Vin_after_fuse: D102.2 (A), F2.2, L1.2, U1.8 (V_{IN})
/Vout: F1.2, J2.2
/Vout_before_fuse: C4.1, D1.1 (K), F1.1, R101.1
GND: 4.7k101.2, C1.2, C4.2, C101.2, J1.2, J2.1, R1.2, R2.2, R4.2, U1.4 (AGND), U1.5 (PGND)
unnamed: 4.7k101.1, C5.2

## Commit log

2025-11-03 NEW COMMENT RAHHHHHH
    [Buck_Boost_main.kicad_pcb]
2025-11-04 Add files via upload
    Testing if Kicad files show with Github Changes
    [MCU.kicad_pcb, MCU.kicad_sch]
2025-11-04 Add files via upload
    Checking again if files show up on Kicad
    [Hall Sensor Schematic.kicad_pcb, Hall Sensor Schematic.kicad_sch]
2025-11-06 Finishing another draft of Inverting Buck
    [Inverting_Buck_Maria.kicad_pcb]
2025-11-06 Made a couple of changes, aligned the gnd and vout terminals of the screw terminal and capacitor so at to have a cleaner and wider vout/gnd copper pour, with buck having a larger Iout>Iin, so less po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
    Also went ahead and drew all the passive components for the IC as closer to the main body of the chip as possible, this will come into greater importance later on when working with more complicated P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
    Via placemnt centralized at the capa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
    [Inverting_Buck_Maria.kicad_pcb]
2025-11-08 Boosr ver1?
    [Boost Practice 1.kicad_pcb, Boost Practice 1.kicad_sch]
2025-11-08 Revert "Boosr ver1?"
    This reverts commit 50cfb5769ac7e5a7e117e2f05ce3dbf4331a3901.
    [Boost Practice 1.kicad_pcb, Boost Practice 1.kicad_sch]
2025-11-08 im tweaking
    [Boost Practice 1.kicad_pcb, Boost Practice 1.kicad_sch]
2025-11-11 Add files via upload
    hello
    [BuckPractice1.kicad_pcb, BuckPractice1.kicad_sch]
2025-11-15 hello 2
    [BuckPractice1.kicad_pcb]
2025-11-16 Folder for buck
    [BuckPractice1.kicad_pcb, BuckPractice1.kicad_sch]
2025-11-20 Maria Boost Practice Schematic
    [BoostPractice1.kicad_pcb, BoostPractice1.kicad_sch]
2025-11-22 Boost PCB Board
    [BoostPractice1.kicad_pcb, BoostPractice1.kicad_sch]
2025-11-22 Add missing vias
    [BoostPractice1.kicad_pcb]
2025-11-22 Schematic only
    [BuckPractice.kicad_pcb, BuckPractice.kicad_sch]
2025-11-22 Revert "Merge branch 'main' of github.com:rsx-electrical/Buck_Boost-24V-"
    This reverts commit 1544c4365805954bfe84498f9553f0563d02ccfb, reversing
    changes made to f300fd34cac0b3ee4a6897acb38f98237bb70485.
    [BoostPractice1.kicad_pcb]
2025-11-22 final for now
    [BuckPractice.kicad_sch]
2025-11-27 final update
    [BuckPractice.kicad_pcb]
2026-01-17 Placed in Inductor, Controller, and Fets, along with obligatory heatsink, screw terms, and fuses.
    I realized that we already have an extra 15uh power inductor from the bucks with very low dcr and high sat current (1.62mohm, 16A), so we can use this one:(PQ2614BHA-150K)
    [Buck_Boost_main.kicad_pcb, Buck_Boost_main.kicad_sch]
2026-01-18 folder restructure
    [Boost Practice 1.kicad_pcb, Boost Practice 1.kicad_sch, BoostPractice1.kicad_pcb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]
2026-01-18 Updated KiCad schematic with selected caps and resistors; saved snapshot to History
    [Buck_Boost_main.kicad_sch]
2026-02-06 main pwr path
    [Buck_Boost_main.kicad_sch]
2026-02-07 Reformat to be human readable
    [Buck_Boost_main.kicad_sch]
2026-02-28 High side switch
    [Buck_Boost_main.kicad_sch]
2026-03-06 Adding filtering capacitance values
    [Buck_Boost_main.kicad_sch]
2026-03-06 Creating LTSpice folder with high side switch test circuit
2026-03-06 LT8390 pins
    [Buck_Boost_main.kicad_sch]
2026-03-08 Update buck boost feedback circuit, add trimmer and decoupling caps
    [Buck_Boost_main.kicad_sch]
2026-03-14 finish up schematic before final check
    [Buck_Boost_main.kicad_sch]
2026-03-14 final schem
    [Buck_Boost_main.kicad_sch]
2026-03-17 Updated Schematic with cool stuff trust
    [Buck_Boost_main.kicad_pcb, Buck_Boost_main.kicad_sch]
2026-04-03 Updated the Component Placement
    [Buck_Boost_main.kicad_pcb]
2026-05-23 pcb - lets pray
    [Buck_Boost_main.kicad_pcb]
2026-06-03 Edited component placement. Added general sketch for the power path. Removed some traces.
    [Buck_Boost_main.kicad_pcb]
2026-06-04 controller and auxiliary circuits
    [Buck_Boost_main.kicad_pcb]
